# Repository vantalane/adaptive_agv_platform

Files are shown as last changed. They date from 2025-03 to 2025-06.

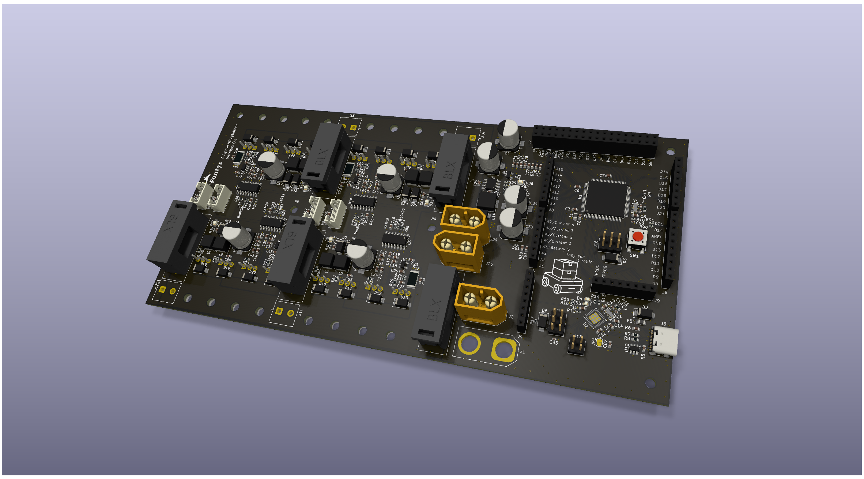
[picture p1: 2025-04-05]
design_sources/KiCAD/controller_mainboard_v0_1/controller_mainboard_visual.png

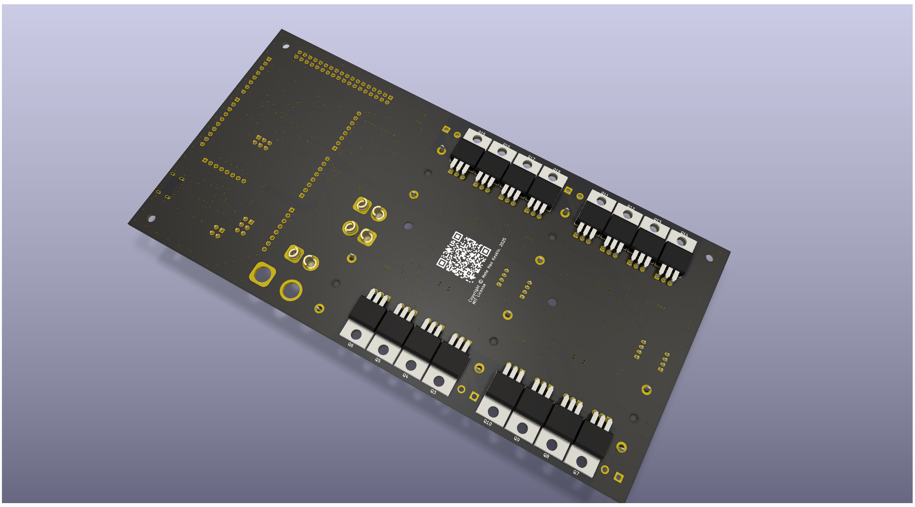
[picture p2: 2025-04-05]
design_sources/KiCAD/controller_mainboard_v0_1/controller_mainboard_visual_bottom.png

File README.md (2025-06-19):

# adaptive_agv_platform
Fontys adaptive robotics AGV platform design repository.

## Design files roadmap

Specifications and board information can be found in the "documentation" folder.

Design sources are aptly placed within design_sources folder. These include kicad files, production files and example code.

## PCBA production

Necessary files and information regarding ordering, assembly and part sourcing are packaged together with PCB versions.

These files can be found within 
``` design_sources/KiCAD/controller_mainboard_vX/production``` \
with ```vX``` being version number.

Instruction for production are found within the ```production``` folder. 
Currently, only V0.1 is available.

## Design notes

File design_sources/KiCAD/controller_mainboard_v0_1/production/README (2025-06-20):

Production files generated by use of Fabrication Toolkit by bennymeg

Order instructions for FONTYS.

PCB is designed with part availability of LCSC and Tinytronics.
The PCB will be assembled by using JLC PCBA service, the order procedure is similar to ordering only PCB's, but with some additions to it.

Steps

1- 
Load the controller_mainboard.zip on the jlcpcb order page.

2- 
From top to bottom, select the following settings:
base material: FR4
layers: 4
Dimensions are automatically filled (200x100mm)
QTY: 5 (This version 0.1 is deemed a prototype, therefore should always be validated before larger orders (a.k.a, buy the V1 largescale))
product type: industrial/consumer

different design: 1
Delivery format: single pcb
thickness: 1.6mm
color: (up to you, green is cheapest and fastest, but purple fits Fontys theme)
Silk: white
Materiel type: FR4-std TG 135-140
Surface finish: LeadFree HASL

Outer copper weight: 1oz
inner copper weight: 0.5oz
Layer sequence: yes
	L1 - controller_mainboard-F_Cu.gtl
	L2 - controller_mainboard-In1_Cu.g1
	L3 - controller_mainboard-In2_Cu.g2
	L4 - controller_mainboard-B_Cu.gbl
Specify stackup: yes - JLC04161H-7628
Via covering: plugged
Min via diameter: 0.3mm/(0.4/0.45mm)
Outline tolerance: regular
Confirm prod file: No
Mark on PCB: Order number
Gold Fingers: no
Castellated hole:no
pressfit hole: no
edge plating: no
Blind slots: no

3- 
Select "PCB Assembly" by using the button.

Fill in the following settings for PCB assembly:

PCBA type: Eco
Assembly side: Top
PCBA QTY: 2
Tooling holes: JLCPCB
Confirm part placement: Yes
Stencil storage: no 
Fixture Storage: no
Parts Selection: customer

*Dont fill in advanced options*
*ignore stencil*

4- 
Proceed by clicking on the "NEXT" button

5-
Now you should get a render of the PCB, proceed by clicking next
*photo here*

6-
Add bom file: bom.csv
Add CPL file: positions.csv
Go to next page after upload.

7- 
Most necessary parts should be automatically automatically selected. If certain parts are out of stock, and therefore are automatically not selected, alternative parts will need to be provided.
In this case, contact an experienced EE or me (m.keskin@student.fontys.nl or mete@kestech.net) for support.

All, EXCEPT for the following should be selected:
*XT-60 AMASS CONNECTOR J2,J25

Thus, at the top of the page you should have:
Total 40 parts detected, 35 parts confirmed, 10 parts not selected

The following are automatically not selected for assembly, 
J1
J7
J8 
J10,J4,J5,J6,J9
J11,J12,J13,J14
J16,J19
J18
J20,J21,J22,J23

Click on "NEXT" and after this "Do not place".

8- 
Now, a render of the PCB files should be displayed. 
*photo*
Click "NEXT".

9- 
On the Quote & order 
Select product description as - Research\Education\DIY\Entertainment > Robot - HS Code 847990

10- Pay

11- After JLC, there are certain parts that will be manually assembled onto the PCB. These are described in the "controller_board_v0_1.ods" spreadsheet file. Here, parts per PCB are described, order multiples of this set according to how many PCB's are going to be assembled.

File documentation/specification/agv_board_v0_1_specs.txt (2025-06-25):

Summary of board capabilites.

PCBA power:
	Battery voltage range: 8.5V - 15V
	Supply current abs max: 20A
	Supply current typical max: 15.2A

	Note: Power supplied by USB-C only powers the microcontrollers and certain current measurement IC's. Avoid powering high power devices through USB. 
 
Safety:
	Emergency stop: A male XT-60 connector is used to pass-through power supplied by a battery. A normally-closed high current emergency stop button should be used to short the terminals of connector J25. If this isn't connected, the battery will be practically "disconnected".

Motor drivers:
	Supply current: 5A absolute max, 3,8A typical max
	Driver voltage: Same as the battery voltage supplying board.
	
Motor current measurement:
	Measured until 5A max
	Voltage per Amp ratio: 1 V/A
	Vcurrent low-pass frequency cutoff(-3db point): 795.77 Hz 

Battery voltage measurement:
	Voltage divider ratio: 0.3377
		Example: Battery is 13.89 volts, Atmega ADC measures 13.89*0.3377=4.69V

Pins described below are additional information or explicit override of the Arduino mega board pins.
The AAP board allocates some GPIO for certain tasks.

Allocated GPIO of Atmega2560:

#Encoder pinouts
D22	ENC_B4
D23	ENC_A4
D24	ENC_B3
D25	ENC_A3
D26	ENC_B2
D27	ENC_A2
D28	ENC_B1
D29	ENC_B1

#Motor driver PWM pinouts
D2	MOT_DRV_PWM_B4
D3	MOT_DRV_PWM_A4
D4	MOT_DRV_PWM_B2
D5	MOT_DRV_PWM_A2
D6	MOT_DRV_PWM_A3
D7	MOT_DRV_PWM_B3
D8	MOT_DRV_PWM_A1
D9	MOT_DRV_PWM_B1

ADC3	VBAT_ADC
ADC4	MOT_CURR_V_1
ADC5	MOT_CURR_V_2
ADC6	MOT_CURR_V_3
ADC7	MOT_CURR_V_4

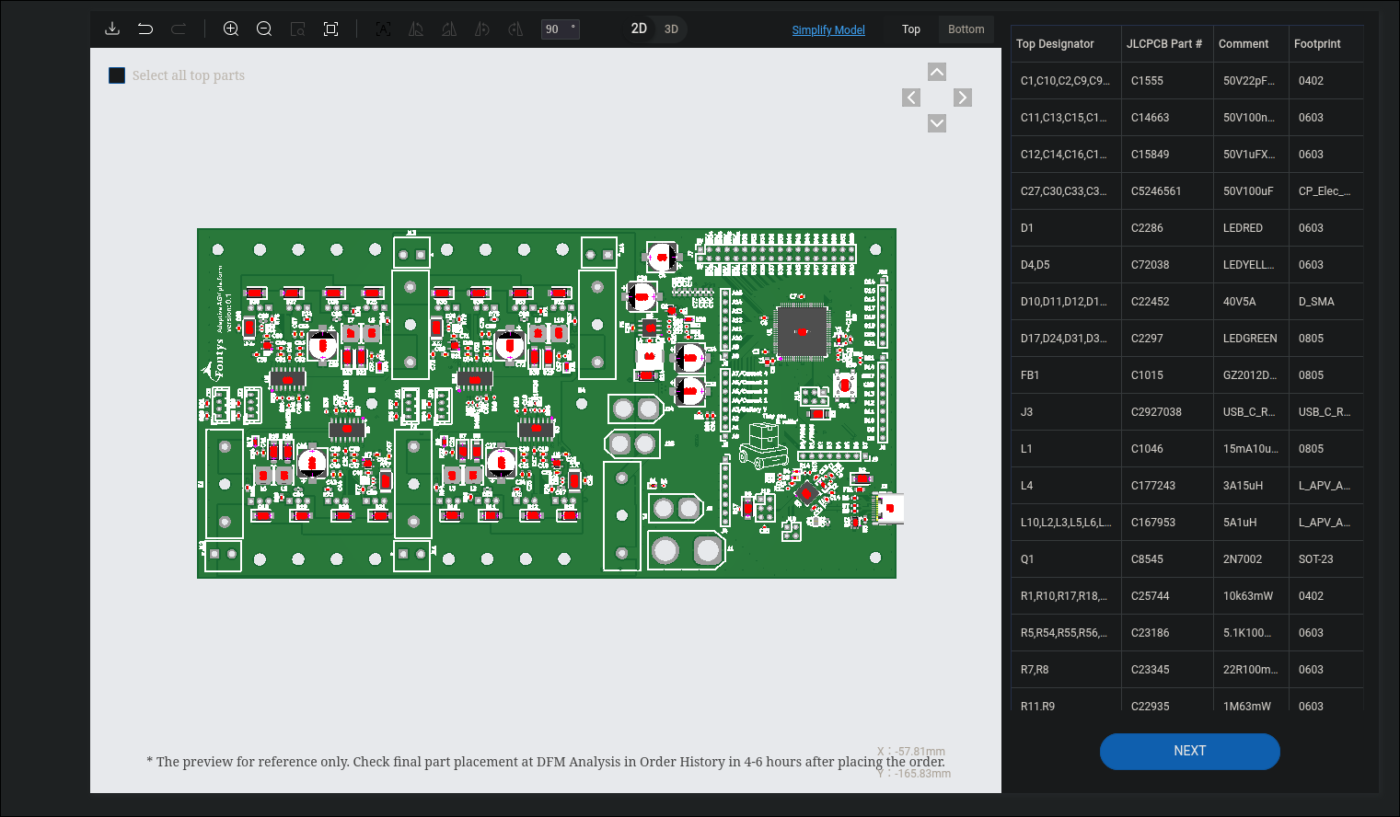
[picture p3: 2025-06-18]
documentation/media/pcba_overview_jlcpcb.png

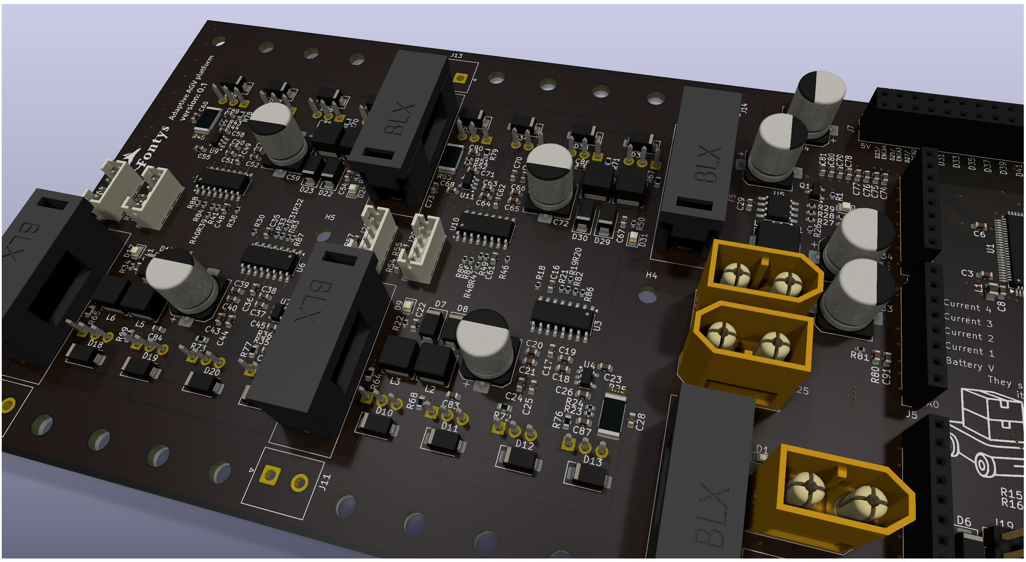
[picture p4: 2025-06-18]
documentation/media/pcba_v1_cool_render.png

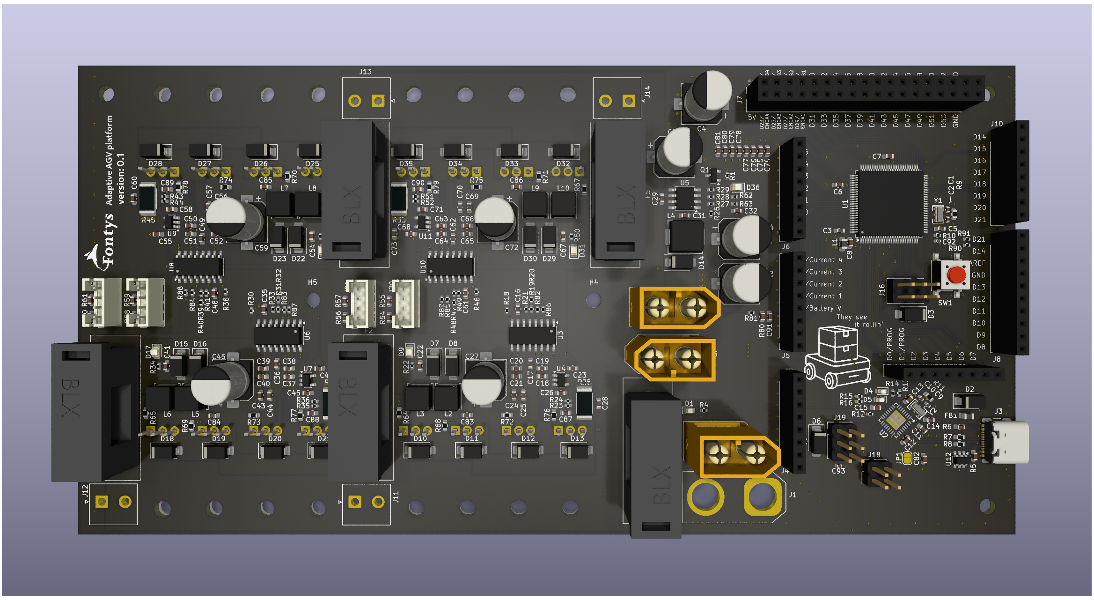
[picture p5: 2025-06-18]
documentation/media/pcba_v1_front_render.png

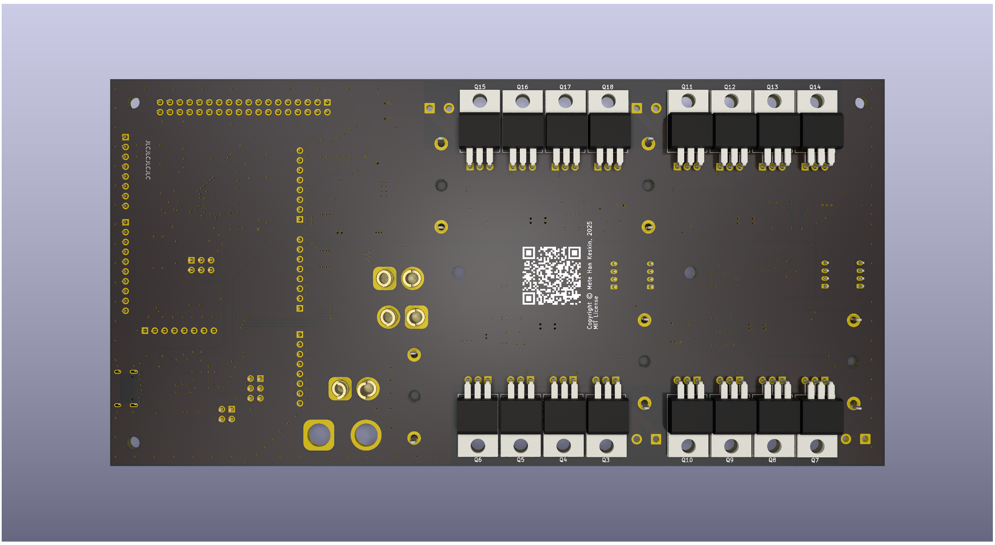
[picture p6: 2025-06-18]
documentation/media/pcba_v1_back_render.png

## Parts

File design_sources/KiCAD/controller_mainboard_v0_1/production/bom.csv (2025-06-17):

Designator | Footprint | Quantity | Value | LCSC Part #
C1, C10, C2, C9, C92, C93 | 0402 | 6 | 50V 22pF C0G | C1555
C11, C13, C15, C17, C23, C26, C28, C3, C31, C36, C42, C45, C47, C49, C5, C55, C58, C6, C60, C62, C68, C71, C73, C8, C91 | 0603 | 25 | 50V 100nF X7R | C14663
C12, C14, C16, C18, C19, C20, C21, C22, C24, C25, C29, C32, C35, C37, C38, C39, C40, C41, C43, C44, C48, C50, C51, C52, C53, C54, C56, C57, C61, C63, C64, C65, C66, C67, C69, C7, C70 | 0603 | 37 | 50V 1uF X5R | C15849
C27, C30, C33, C34, C4, C46, C59, C72 | CP_Elec_8x10.5 | 8 | 50V 100uF | C5246561
D1 | 0603 | 1 | LED RED | C2286
D10, D11, D12, D13, D14, D15, D16, D18, D19, D2, D20, D21, D22, D23, D25, D26, D27, D28, D29, D3, D30, D32, D33, D34, D35, D6, D7, D8 | D_SMA | 28 | 40V 5A | C22452
D17, D24, D31, D36, D9 | 0805 | 5 | LED GREEN | C2297
D4, D5 | 0603 | 2 | LED YELLOW | C72038
F1 | BLX-A fuse holder | 1 | Fuse 20A
F2, F3, F4, F5 | BLX-A fuse holder | 4 | 5A
FB1 | 0805 | 1 | GZ2012D101TF | C1015
J1 | XT-90_Connector | 1 | XT-90
J10, J4, J5, J6, J9 | PinSocket_1x08_P2.54mm_Vertical | 5 | 01x08_2.54mm _socket
J11, J12, J13, J14 | JST_NV_B02P-NV_1x02_P5.00mm_Vertical | 4 | 2P_screw_term
J16, J19 | PinHeader_2x03_P2.54mm_Vertical | 2 | 02x03_pinheader
J18 | PinHeader_2x02_P2.54mm_Vertical | 1 | 02x02_pinheader
J2, J25 | AMASS_XT60-M_1x02_P7.20mm_Vertical | 2 | XT-60
J20, J21, J22, J23 | JST_PH_B4B-PH-K_1x04_P2.00mm_Vertical | 4 | 01x04_JST_PH
J3 | USB_C_Receptacle_GCT_USB4105-xx-A_16P_TopMnt_Horizontal | 1 | USB_C_Receptacle_USB2.0_16P | C2927038
J7 | PinSocket_2x18_P2.54mm_Vertical | 1 | 02x18_2.54mm_socket
J8 | PinSocket_1x10_P2.54mm_Vertical | 1 | Conn_01x10_2.54mm_socket
L1 | 0805 | 1 | 15mA 10uH 1.15Ohm | C1046
L10, L2, L3, L5, L6, L7, L8, L9 | L_APV_ANR5040 | 8 | 5A 1uH | C167953
L4 | L_APV_APH0630 | 1 | 3A 15uH | C177243
Q1 | SOT-23 | 1 | 2N7002 | C8545
Q10, Q11, Q12, Q13, Q14, Q15, Q16, Q17, Q18, Q3, Q4, Q5, Q6, Q7, Q8, Q9 | TO-220-3_Horizontal_TabDown | 16 | IRF3205 | C2561
R1, R10, R17, R18, R19, R20, R26, R27, R28, R29, R30, R31, R32, R38, R39, R40, R46, R47, R48, R81, R82, R83, R84, R85, R86, R87, R88, R89, R90, R91 | 0402 | 30 | 10k 63mW | C25744
R11, R9 | 0603 | 2 | 1M 63mW | C22935
R12, R13, R14, R15, R16, R22, R23, R24, R34, R35, R36, R4, R42, R43, R44, R50, R51, R52, R62, R63 | 0402 | 20 | 1k 63mW | C11702
R25, R37, R45, R53 | 2512 | 4 | 50m 750mW 1% | C127698
R5, R54, R55, R56, R57, R58, R59, R6, R60, R61, R80 | 0603 | 11 | 5.1K 100mW | C23186
R64, R65, R66, R67, R68, R69, R70, R71, R72, R73, R74, R75, R76, R77, R78, R79 | 0603 | 16 | 0R 100mW | C21189
R7, R8 | 0603 | 2 | 22R 100mW | C23345
SW1 | SW_SPST_PTS645 | 1 | SW_Push | C19191552
U1 | TQFP-100_14x14mm_P0.5mm | 1 | ATmega2560-16A | C22460
U10, U3, U6, U8 | SOIC-16_3.9x9.9mm_P1.27mm | 4 | HIP4082IBZT | C50123
U11, U4, U7, U9 | SOT-23-5 | 4 | INA180A1IDBVR | C122228
U12 | SOT-23-6 | 1 | USBLC6-4SC6 | C5180279
U2 | QFN-32-1EP_5x5mm_P0.5mm_EP3.1x3.1mm | 1 | ATmega16U2-M | C17317
U5 | TI_SO-PowerPAD-8_ThermalVias | 1 | TPS5430DDA | C9864
Y1, Y2 | Resonator_SMD_Murata_CSTxExxV-3Pin_3.0x1.1mm | 2 | 16MHz | C783275

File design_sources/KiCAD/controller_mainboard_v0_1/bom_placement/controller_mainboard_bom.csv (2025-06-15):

Id | Designator | Footprint | Quantity | Designation | Supplier and ref
1 | U12 | SOT-23-6 | 1 | USBLC6-4SC6
2 | C11,C47,C45,C5,C42,C3,C6,C68,C26,C15,C8,C60,C13,C58,C71,C23,C91,C62,C17,C55,C36,C31,C49,C28,C73 | C_0603_1608Metric | 25 | 50V 100nF X7R
3 | J6,J5,J9,J4,J10 | PinSocket_1x08_P2.54mm_Vertical | 5 | 01x08_2.54mm _socket
4 | R17,R29,R30,R82,R85,R20,R28,R47,R46,R88,R10,R27,R31,R39,R48,R40,R19,R81,R26,R32,R1,R86,R84,R90,R87,R38,R91,R83,R18,R89 | R_0402_1005Metric | 30 | 10k 63mW
5 | D21,D8,D34,D33,D18,D22,D12,D26,D28,D15,D19,D10,D27,D25,D20,D11,D14,D35,D32,D23,D30,D16,D7,D3,D6,D13,D2,D29 | D_SMA | 28 | 40V 5A
6 | J16,J19 | PinHeader_2x03_P2.54mm_Vertical | 2 | 02x03_pinheader
7 | C82,C85,C78,C89,C83,C90,C88,C74,C87,C84,C80,C76,C79,C75,C77,C81,C86 | C_0603_1608Metric | 17 | N.C.
8 | U7,U4,U11,U9 | SOT-23-5 | 4 | INA180A1IDBVR
9 | C53,C65,C20,C56,C52,C14,C66,C24,C18,C50,C54,C35,C22,C43,C37,C70,C12,C19,C63,C67,C32,C40,C41,C16,C7,C57,C25,C61,C38,C29,C51,C64,C21,C44,C39,C69,C48 | C_0603_1608Metric | 37 | 50V 1uF X5R
10 | D17,D31,D36,D24,D9 | LED_0805_2012Metric | 5 | LED GREEN
11 | R33,R49,R41,R21 | R_0402_1005Metric | 4 | N.C.
12 | L3,L2,L9,L5,L10,L7,L8,L6 | L_APV_ANR5040 | 8 | 5A 1uH
13 | C1,C2,C93,C92,C9,C10 | C_0402_1005Metric | 6 | 50V 22pF C0G
14 | R15,R34,R50,R24,R44,R14,R63,R43,R52,R23,R42,R36,R62,R12,R16,R4,R22,R35,R51,R13 | R_0402_1005Metric | 20 | 1k 63mW
15 | F2,F4,F3,F5 | BLX-A fuse holder | 4 | 5A
16 | C46,C34,C4,C59,C27,C30,C33,C72 | CP_Elec_8x10.5 | 8 | 50V 100uF
17 | J12,J13,J14,J11 | JST_NV_B02P-NV_1x02_P5.00mm_Vertical | 4 | 2P_screw_term
18 | R60,R56,R54,R57,R6,R59,R61,R58,R80,R55,R5 | C_0603_1608Metric | 11 | 5.1K 100mW
19 | D1 | LED_0603_1608Metric | 1 | LED RED
20 | F1 | BLX-A fuse holder | 1 | Fuse 20A
21 | U6,U3,U8,U10 | SOIC-16_3.9x9.9mm_P1.27mm | 4 | HIP4082IBZT
22 | U5 | TI_SO-PowerPAD-8_ThermalVias | 1 | TPS5430DDA
23 | J25,J2,J24 | AMASS_XT60-M_1x02_P7.20mm_Vertical | 3 | XT-60
24 | D5,D4 | LED_0603_1608Metric | 2 | LED YELLOW
25 | R76,R66,R64,R71,R78,R74,R69,R75,R72,R67,R70,R77,R68,R79,R65,R73 | R_0603_1608Metric | 16 | 0R 100mW
26 | J22,J21,J23,J20 | JST_PH_B4B-PH-K_1x04_P2.00mm_Vertical | 4 | 01x04_JST_PH
27 | L1 | L_0805_2012Metric | 1 | 15mA 10uH 1.15Ohm
28 | Q1 | SOT-23 | 1 | 2N7002
29 | R37,R25,R53,R45 | R_2512_6332Metric | 4 | 50m 750mW 1%
30 | Y1,Y2 | Resonator_SMD_Murata_CSTxExxV-3Pin_3.0x1.1mm | 2 | 16MHz
31 | U2 | QFN-32-1EP_5x5mm_P0.5mm_EP3.1x3.1mm | 1 | ATmega16U2-M
32 | U1 | TQFP-100_14x14mm_P0.5mm | 1 | ATmega2560-16A
33 | J8 | PinSocket_1x10_P2.54mm_Vertical | 1 | Conn_01x10_2.54mm_socket
34 | J1 | XT-90_Connector | 1 | XT-90
35 | R7,R8 | R_0603_1608Metric | 2 | 22R 100mW
36 | SW1 | SW_SPST_PTS645 | 1 | SW_Push
37 | J3 | USB_C_Receptacle_GCT_USB4105-xx-A_16P_TopMnt_Horizontal | 1 | USB_C_Receptacle_USB2.0_16P
38 | J7 | PinSocket_2x18_P2.54mm_Vertical | 1 | 02x18_2.54mm_socket
39 | L4 | L_APV_APH0630 | 1 | 3A 15uH
40 | R9,R11 | R_0603_1608Metric | 2 | 1M 63mW
41 | J18 | PinHeader_2x02_P2.54mm_Vertical | 1 | 02x02_pinheader
42 | FB1 | L_0805_2012Metric | 1 | GZ2012D101TF
43 | Q9,Q4,Q8,Q6,Q11,Q14,Q13,Q7,Q15,Q10,Q18,Q3,Q16,Q5,Q12,Q17 | TO-220-3_Horizontal_TabDown | 16 | IRF3205

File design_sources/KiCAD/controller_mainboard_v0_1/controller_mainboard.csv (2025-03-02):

Reference | Qty | JLCPCB | Value | DNP | Exclude from BOM | Exclude from Board | Footprint | Datasheet
C1,C2,C8,C9 | 4 | C1555 | 50V 22pF C0G |  |  |  | Capacitor_SMD:C_0402_1005Metric | https://jlcpcb.com/api/file/downloadByFileSystemAccessId/8579707297419231232
C3,C6,C11,C13,C19,C20,C22,C23,C24,C25,C26,C27,C33,C34 | 14 | C15849 | 50V 1uF X5R |  |  |  | Capacitor_SMD:C_0603_1608Metric | https://jlcpcb.com/api/file/downloadByFileSystemAccessId/8556213788459761664
C4,C5,C7,C10,C12,C14,C15,C16,C17,C18,C28,C29 | 12 | C14663 | 50V 100nF X7R |  |  |  | Capacitor_SMD:C_0603_1608Metric | https://jlcpcb.com/api/file/downloadByFileSystemAccessId/8579707083955945472
C21,C30,C31,C32 | 4 | C5246561 | 50V 100uF |  |  |  | Capacitor_SMD:CP_Elec_8x10.5 | ~
D1,D2,D5,D6,D7,D8,D9,D10,D11,D12 | 10 | C22452 | 40V 5A |  |  |  | Diode_SMD:D_SMA | https://jlcpcb.com/api/file/downloadByFileSystemAccessId/8579707587489042432
D3,D4 | 2 | C72038 | LED YELLOW |  |  |  | LED_SMD:LED_0603_1608Metric | ~
F1 | 1 |  | Fuse 20A |  |  |  | Custom_feetprint:BLX-A fuse holder | ~
F2 | 1 |  | 5A |  |  |  | Custom_feetprint:BLX-A fuse holder | ~
FB1 | 1 | C1015 | GZ2012D101TF |  |  |  | Inductor_SMD:L_0805_2012Metric | https://jlcpcb.com/api/file/downloadByFileSystemAccessId/8579709135115370496
J1,J4 | 2 |  | 02x03_pinheader |  |  |  | Connector_PinHeader_2.54mm:PinHeader_2x03_P2.54mm_Vertical | ~
J2 | 1 |  | 01x05_Socket | DNP | Excluded from BOM |  |  | ~
J3 | 1 |  | 02x02_pinheader |  |  |  |  | ~
J5 | 1 |  | XT-90 |  |  |  |  | ~
J6 | 1 |  | USB_C_Receptacle_USB2.0_16P |  |  |  |  | https://www.usb.org/sites/default/files/documents/usb_type-c.zip
J7 | 1 |  | XT-60 |  |  |  |  | ~
JP2 | 1 |  | SolderJumper_2_Open |  | Excluded from BOM |  | Jumper:SolderJumper-2_P1.3mm_Open_RoundedPad1.0x1.5mm | ~
L1 | 1 | C1046 | 15mA 10uH 1.15Ohm |  |  |  | Inductor_SMD:L_0805_2012Metric | ~
L2,L3 | 2 | C167953 | 5A 1uH |  |  |  |  | ~
L4 | 1 | C177243 | 3A 15uH |  |  |  |  | ~
Q1,Q2,Q3,Q4 | 4 | C2561 | IRF3205 |  |  |  | Package_TO_SOT_THT:TO-220-3_Vertical | http://www.irf.com/product-info/datasheets/data/irf3205.pdf
Q5 | 1 | C8545 | 2N7002 |  |  |  | Package_TO_SOT_SMD:SOT-23 | https://www.onsemi.com/pub/Collateral/NDS7002A-D.PDF
R1,R9,R13,R14,R16,R19,R20,R21,R22,R23 | 10 | C25744 | 10k 63mW |  |  |  | Resistor_SMD:R_0402_1005Metric | https://jlcpcb.com/api/file/downloadByFileSystemAccessId/8556212101498380288
R2,R8 | 2 |  | 1M 63mW |  |  |  | Resistor_SMD:R_0603_1608Metric | ~
R3,R4,R5,R6,R7,R11,R12 | 7 | C11702 | 1k 63mW |  |  |  | Resistor_SMD:R_0402_1005Metric
R10 | 1 | C620706 | 50m 750mW 1% |  |  |  | Resistor_SMD:R_2512_6332Metric | ~
R15 | 1 | C25744 | N.C. | DNP |  |  | Resistor_SMD:R_0402_1005Metric | https://jlcpcb.com/api/file/downloadByFileSystemAccessId/8556212101498380288
R17,R18 | 2 | C23345 | 22R 100mW |  |  |  | Resistor_SMD:R_0603_1608Metric | ~
U1 | 1 |  | ATmega2560-16A |  |  |  | Package_QFP:TQFP-100_14x14mm_P0.5mm | http://ww1.microchip.com/downloads/en/DeviceDoc/Atmel-2549-8-bit-AVR-Microcontroller-ATmega640-1280-1281-2560-2561_datasheet.pdf
U2 | 1 |  | ATmega16U2-M |  |  |  | Package_DFN_QFN:QFN-32-1EP_5x5mm_P0.5mm_EP3.1x3.1mm | http://ww1.microchip.com/downloads/en/DeviceDoc/doc7799.pdf
U3 | 1 | C50123 | HIP4082IBZT |  |  |  | Package_SO:SOIC-16_3.9x9.9mm_P1.27mm | https://www.renesas.com/www/doc/datasheet/hip4082.pdf
U4 | 1 | C122228 | INA180A1IDBVR |  |  |  | Package_TO_SOT_SMD:SOT-23-5 | http://www.ti.com/lit/ds/symlink/ina180.pdf
U5 | 1 | C9864 | TPS5430DDA |  |  |  | Package_SO:TI_SO-PowerPAD-8_ThermalVias | http://www.ti.com/lit/ds/symlink/tps5430.pdf
Y2,Y3 | 2 | C783275 | 16MHz |  |  |  | Crystal:Resonator_SMD_Murata_CSTxExxV-3Pin_3.0x1.1mm | ~

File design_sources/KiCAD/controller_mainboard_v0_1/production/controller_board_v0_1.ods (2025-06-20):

PART MFR | DESC. | QTY (P/PCB) | SELLER | ALL QTY COST | PART COST (ex BTW) | URL
005974 | JST-PH 4P cable | 4 | Tinytronics | 2.64 | 0.66 | https://www.tinytronics.nl/en/cables-and-connectors/cables-and-adapters/jst-compatible/jst-ph-female-to-dupont-female-compatible-cable-4p-15cm
001195 | Fuse holder 5x20mm - 5A – PCB | 5 | Tinytronics | 2.05 | 0.41 | https://www.tinytronics.nl/en/components/fuses/fuse-holder-5x20mm-5a-pcb
000504 | 8 Pins header Female | 5 | Tinytronics | 0.9 | 0.18 | https://www.tinytronics.nl/en/cables-and-connectors/connectors/pin-headers/female/8-pins-header-female
001181 | 2x18 Pins header Female | 1 | Tinytronics | 0.36 | 0.36 | https://www.tinytronics.nl/en/cables-and-connectors/connectors/pin-headers/female/2x18-pins-header-female
000506 | 10 Pins header Female | 1 | Tinytronics | 0.21 | 0.21 | https://www.tinytronics.nl/en/cables-and-connectors/connectors/pin-headers/female/10-pins-header-female
000170 | 2 Pin Screw Terminal Block Connector 5.08mm Distance | 4 | Tinytronics | 2.48 | 0.62 | https://www.tinytronics.nl/en/cables-and-connectors/connectors/screw-terminals/2-pin-screw-terminal-block-connector-5.08mm-distance
 | 2x3 male pins | 2 | T.B.D | 0
 | 2x2 male pins | 1 | T.B.D | 0
002382 | XT60U connector set | 2 | Tinytronics | 1.48 | 0.74
 |  |  |  | 0
 |  |  |  | 0
 |  |  |  | 0
 |  |  |  | 0
 |  |  |  | 0
 |  |  |  | 0
 |  |  |  | 0
 |  |  |  | 0
 |  |  |  | 0
 |  |  |  | 0
Total cost of 1 PCB | 10.12

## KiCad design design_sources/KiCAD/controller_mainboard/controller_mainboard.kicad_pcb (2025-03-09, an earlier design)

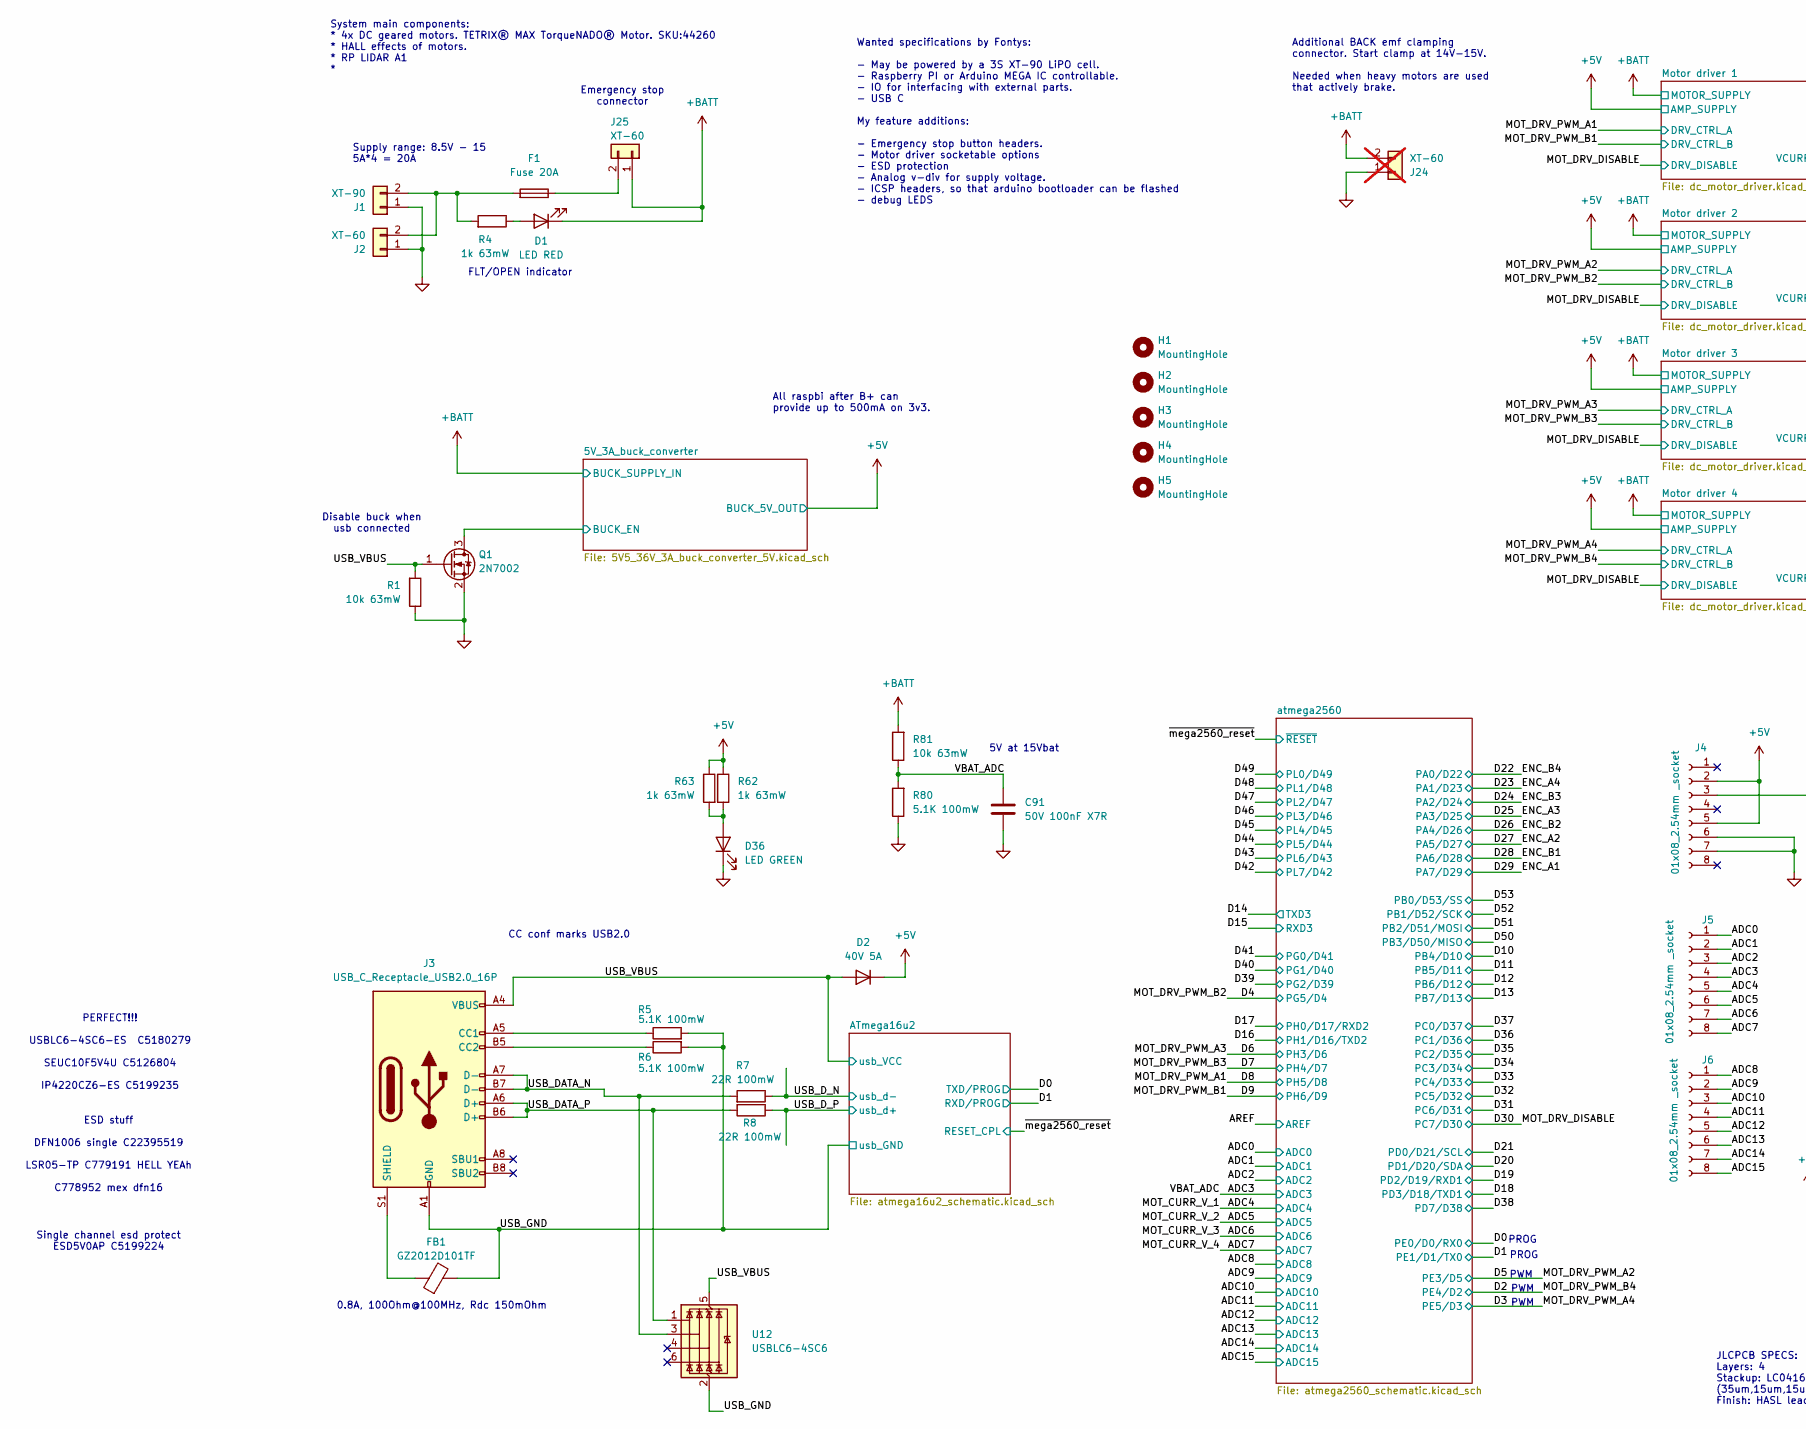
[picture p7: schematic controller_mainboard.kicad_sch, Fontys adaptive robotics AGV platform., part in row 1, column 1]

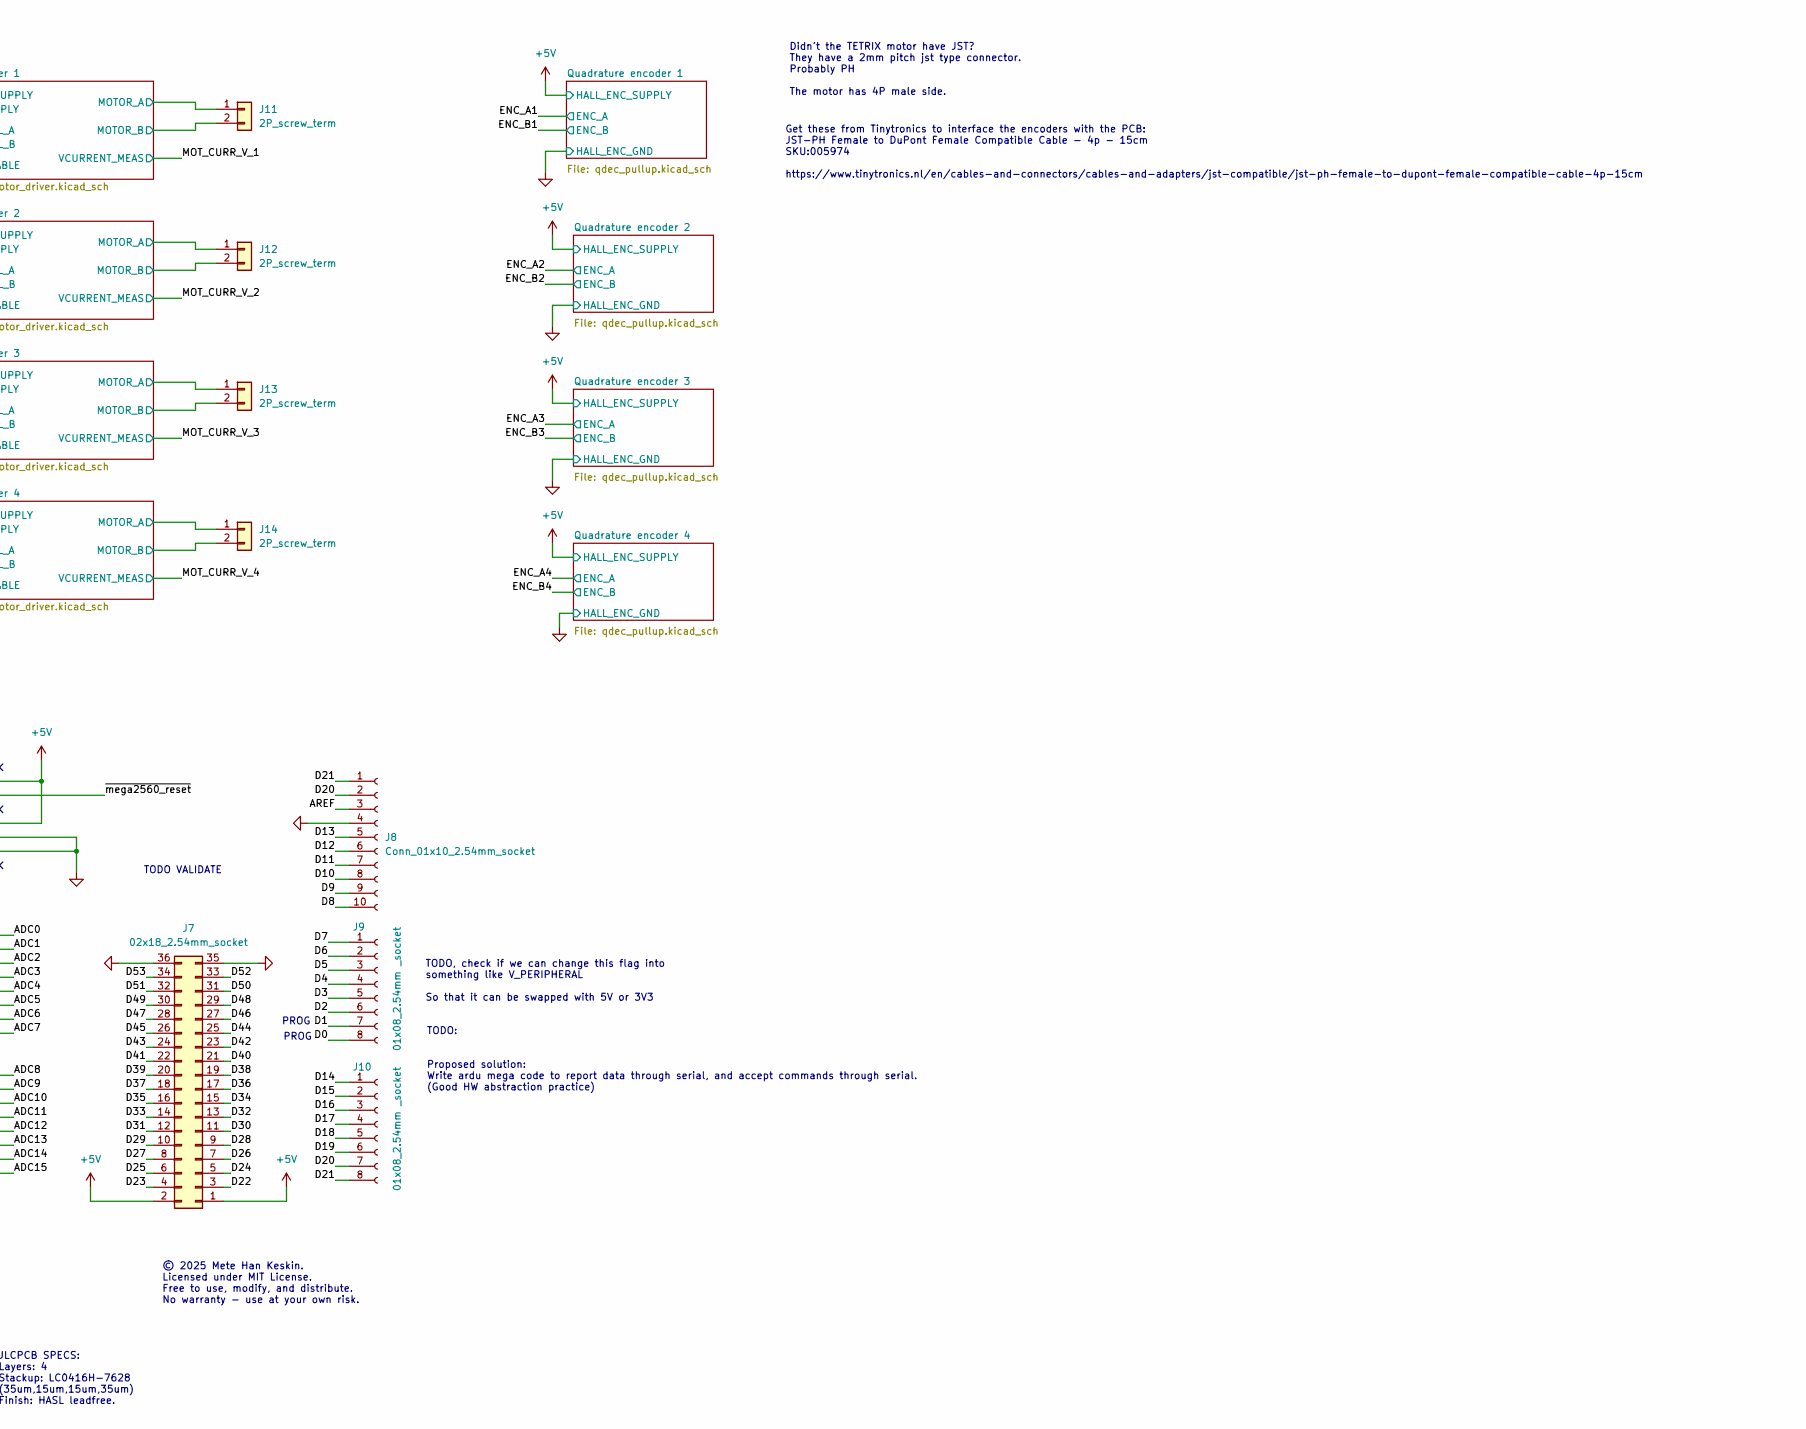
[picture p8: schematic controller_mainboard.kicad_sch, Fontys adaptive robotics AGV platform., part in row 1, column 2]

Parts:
C91: 50V 100nF X7R; C_0603_1608Metric; LCSC C14663
D1: LED RED; LED_0603_1608Metric; LCSC C2286
D2: 40V 5A; D_SMA; LCSC C22452
D36: LED GREEN; LED_0805_2012Metric; LCSC C2297
F1: Fuse 20A; BLX-A fuse holder
FB1: GZ2012D101TF; L_0805_2012Metric; LCSC C1015
H1, H2, H3, H4, H5: MountingHole; MountingHole_3.2mm_M3_DIN965
J1: XT-90; XT-90_Connector
J2: XT-60; AMASS_XT60-M_1x02_P7.20mm_Vertical
J3: USB_C_Receptacle_USB2.0_16P; USB_C_Receptacle_GCT_USB4105-xx-A_16P_TopMnt_Horizontal; LCSC C2927038
J4, J5, J6, J9, J10: 01x08_2.54mm _socket; PinSocket_1x08_P2.54mm_Vertical
J7: 02x18_2.54mm_socket; PinSocket_2x18_P2.54mm_Vertical
J8: Conn_01x10_2.54mm_socket; PinSocket_1x10_P2.54mm_Vertical
J11, J12, J13, J14: 2P_screw_term; JST_NV_B02P-NV_1x02_P5.00mm_Vertical
J24: XT-60; AMASS_XT60-F_1x02_P7.20mm_Vertical; not fitted
J25: XT-60; AMASS_XT60-F_1x02_P7.20mm_Vertical
Q1: 2N7002; SOT-23; LCSC C8545
R1, R81: 10k 63mW; R_0402_1005Metric; LCSC C25744
R4, R62, R63: 1k 63mW; R_0402_1005Metric; LCSC C11702
R5, R6, R80: 5.1K 100mW; C_0603_1608Metric; LCSC C23186
R7, R8: 22R 100mW; R_0603_1608Metric; LCSC C23345
U12: USBLC6-4SC6; SOT-23-6; LCSC C5180279

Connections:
+5V: D2.1 (K), J4.2, J4.5, J7.1, J7.2, R62.1, R63.1; also elsewhere on the board
+BATT: D1.1 (K), J24.2, J25.1, R81.2; also elsewhere on the board
/5V_3A_buck_converter/BUCK_EN: Q1.3 (D); also elsewhere on the board
/ADC0: J5.1; also elsewhere on the board
/ADC1: J5.2; also elsewhere on the board
/ADC2: J5.3; also elsewhere on the board
/ADC4: J5.5; also elsewhere on the board
/ADC5: J5.6; also elsewhere on the board
/ADC6: J5.7; also elsewhere on the board
/ADC7: J5.8; also elsewhere on the board
/ADC8: J6.1; also elsewhere on the board
/ADC9: J6.2; also elsewhere on the board
/ADC10: J6.3; also elsewhere on the board
/ADC11: J6.4; also elsewhere on the board
/ADC12: J6.5; also elsewhere on the board
/ADC13: J6.6; also elsewhere on the board
/ADC14: J6.7; also elsewhere on the board
/ADC15: J6.8; also elsewhere on the board
/AREF: J8.3; also elsewhere on the board
/D0: J9.8; also elsewhere on the board
/D1: J9.7; also elsewhere on the board
/D2: J9.6; also elsewhere on the board
/D3: J9.5; also elsewhere on the board
/D4: J9.4; also elsewhere on the board
/D5: J9.3; also elsewhere on the board
/D6: J9.2; also elsewhere on the board
/D7: J9.1; also elsewhere on the board
/D8: J8.10; also elsewhere on the board
/D9: J8.9; also elsewhere on the board
/D10: J8.8; also elsewhere on the board
/D11: J8.7; also elsewhere on the board
/D12: J8.6; also elsewhere on the board
/D13: J8.5; also elsewhere on the board
/D14: J10.1; also elsewhere on the board
/D15: J10.2; also elsewhere on the board
/D16: J10.3; also elsewhere on the board
/D17: J10.4; also elsewhere on the board
/D18: J10.5; also elsewhere on the board
/D19: J10.6; also elsewhere on the board
/D20: J8.2, J10.7; also elsewhere on the board
/D21: J8.1, J10.8; also elsewhere on the board
/D22: J7.3; also elsewhere on the board
/D23: J7.4; also elsewhere on the board
/D24: J7.5; also elsewhere on the board
/D25: J7.6; also elsewhere on the board
/D26: J7.7; also elsewhere on the board
/D27: J7.8; also elsewhere on the board
/D28: J7.9; also elsewhere on the board
/D29: J7.10; also elsewhere on the board
/D30: J7.11; also elsewhere on the board
/D31: J7.12; also elsewhere on the board
/D32: J7.13; also elsewhere on the board
/D33: J7.14; also elsewhere on the board
/D34: J7.15; also elsewhere on the board
/D35: J7.16; also elsewhere on the board
/D36: J7.17; also elsewhere on the board
/D37: J7.18; also elsewhere on the board
/D38: J7.19; also elsewhere on the board
/D39: J7.20; also elsewhere on the board
/D40: J7.21; also elsewhere on the board
/D41: J7.22; also elsewhere on the board
/D42: J7.23; also elsewhere on the board
/D43: J7.24; also elsewhere on the board
/D44: J7.25; also elsewhere on the board
/D45: J7.26; also elsewhere on the board
/D46: J7.27; also elsewhere on the board
/D47: J7.28; also elsewhere on the board
/D48: J7.29; also elsewhere on the board
/D49: J7.30; also elsewhere on the board
/D50: J7.31; also elsewhere on the board
/D51: J7.32; also elsewhere on the board
/D52: J7.33; also elsewhere on the board
/D53: J7.34; also elsewhere on the board
/Motor driver 1/MOT_SIDE_A: J11.1; also elsewhere on the board
/Motor driver 1/MOT_SIDE_B: J11.2; also elsewhere on the board
/Motor driver 2/MOT_SIDE_A: J12.1; also elsewhere on the board
/Motor driver 2/MOT_SIDE_B: J12.2; also elsewhere on the board
/Motor driver 3/MOT_SIDE_A: J13.1; also elsewhere on the board
/Motor driver 3/MOT_SIDE_B: J13.2; also elsewhere on the board
/Motor driver 4/MOT_SIDE_A: J14.1; also elsewhere on the board
/Motor driver 4/MOT_SIDE_B: J14.2; also elsewhere on the board
/USB_DATA_N: J3.A7 (D-), J3.B7 (D-), R7.2, U12.3 (I/O2)
/USB_DATA_P: J3.A6 (D+), J3.B6 (D+), R8.2, U12.1 (I/O1)
/USB_D_N: R7.1; also elsewhere on the board
/USB_D_P: R8.1; also elsewhere on the board
/USB_GND: FB1.2, J3.A1 (GND), J3.A12 (GND), J3.B1 (GND), J3.B12 (GND), R5.2, R6.2, U12.2 (GND); also elsewhere on the board
/USB_VBUS: D2.2 (A), J3.A4 (VBUS), J3.A9 (VBUS), J3.B4 (VBUS), J3.B9 (VBUS), Q1.1 (G), R1.2, U12.5 (VBUS); also elsewhere on the board
/~mega2560_reset: J4.3; also elsewhere on the board
GND: C91.1, D36.1 (K), J1.1, J2.1, J4.6, J4.7, J7.35, J7.36, J8.4, J24.1, Q1.2 (S), R1.1, R80.1; also elsewhere on the board
unnamed: D1.2 (A), R4.1
unnamed: D36.2 (A), R62.2, R63.2
unnamed: F1.2, J1.2, J2.2, R4.2
unnamed: J3.A5 (CC1), R5.1
unnamed: J3.B5 (CC2), R6.1
unnamed: FB1.1, J3.S1 (SHIELD)
unnamed: F1.1, J25.2

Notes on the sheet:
Get these from Tinytronics to interface the encoders with the PCB: JST-PH Female to DuPont Female Compatible Cable - 4p - 15cm SKU:005974 https://www.tinytronics.nl/en/cables-and-connectors/cables-and-adapters/jst-compatible/jst-ph-female-to-dupont-female-compatible-cable-4p-15cm
PROG
JLCPCB SPECS: Layers: 4 Stackup: LC0416H-7628 (35um,15um,15um,35um) Finish: HASL leadfree.
Emergency stop connector
Wanted specifications by Fontys: - May be powered by a 3S XT-90 LiPO cell. - Raspberry PI or Arduino MEGA IC controllable. - IO for interfacing with external parts. - USB C My feature additions: - Emergency stop button headers. - Motor driver socketable options - ESD protection - Analog v-div for s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
© 2025 Mete Han Keskin. Licensed under MIT License. Free to use, modify, and distribute. No warranty - use at your own risk.
5A*4 = 20A
PWM
ESD stuff DFN1006 single C22395519 LSR05-TP C779191 HELL YEAh C778952 mex dfn16
0.8A, 100Ohm@100MHz, Rdc 150mOhm
TODO VALIDATE
Supply range: 8.5V - 15
All raspbi after B+ can provide up to 500mA on 3v3.
FLT/OPEN indicator
CC conf marks USB2.0
System main components: * 4x DC geared motors. TETRIX® MAX TorqueNADO® Motor. SKU:44260 * HALL effects of motors. * RP LIDAR A1 *
Disable buck when usb connected
TODO: Proposed solution: Write ardu mega code to report data through serial, and accept commands through serial. (Good HW abstraction practice)
Didn't the TETRIX motor have JST? They have a 2mm pitch jst type connector. Probably PH The motor has 4P male side.
PERFECT!!! USBLC6-4SC6-ES C5180279 SEUC10F5V4U C5126804 IP4220CZ6-ES C5199235
5V at 15Vbat
TODO, check if we can change this flag into something like V_PERIPHERAL So that it can be swapped with 5V or 3V3
Single channel esd protect ESD5V0AP C5199224
Additional BACK emf clamping connector. Start clamp at 14V-15V. Needed when heavy motors are used that actively brake.

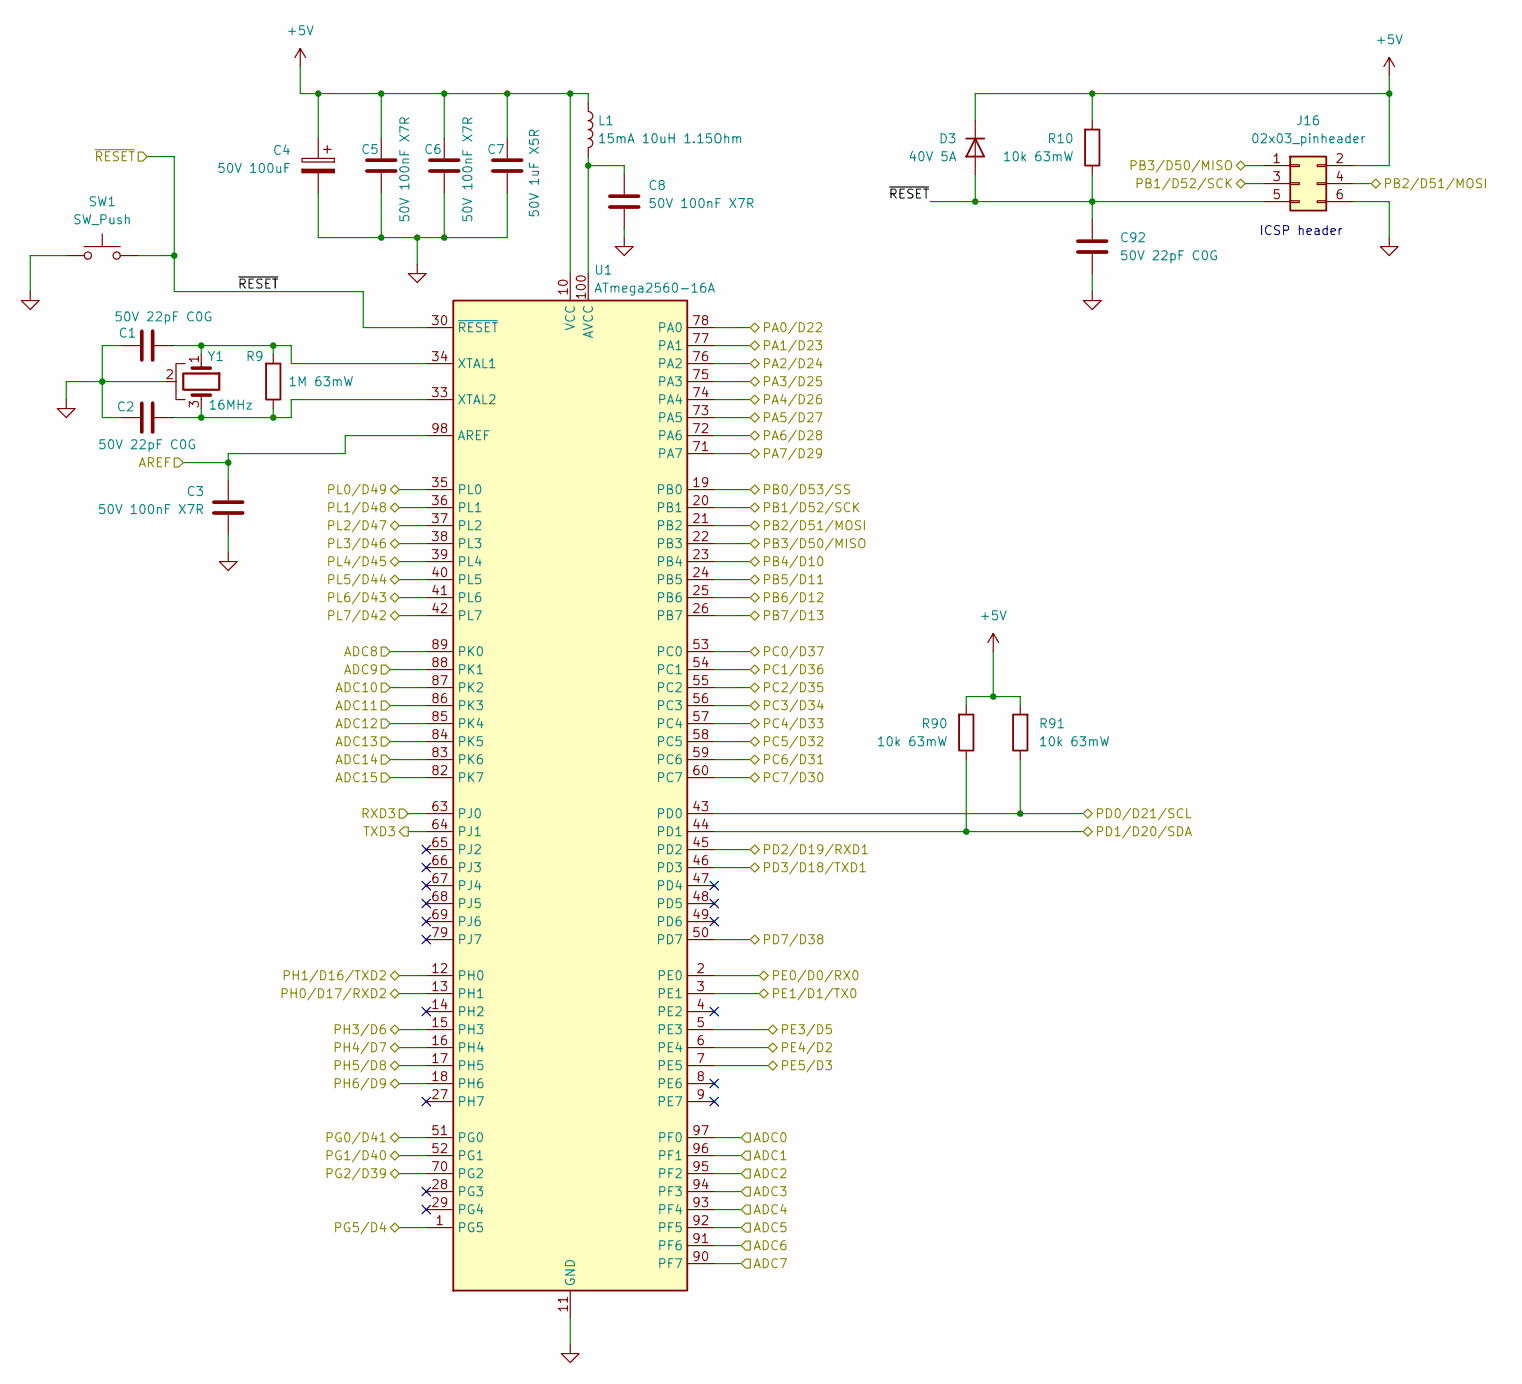
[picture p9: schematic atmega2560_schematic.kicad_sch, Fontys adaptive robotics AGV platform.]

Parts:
C1, C2, C92: 50V 22pF C0G; C_0402_1005Metric; LCSC C1555
C3, C5, C6, C8: 50V 100nF X7R; C_0603_1608Metric; LCSC C14663
C4: 50V 100uF; CP_Elec_8x10.5; LCSC C5246561
C7: 50V 1uF X5R; C_0603_1608Metric; LCSC C15849
D3: 40V 5A; D_SMA; LCSC C22452
J16: 02x03_pinheader; PinHeader_2x03_P2.54mm_Vertical
L1: 15mA 10uH 1.15Ohm; L_0805_2012Metric; LCSC C1046
R9: 1M 63mW; R_0603_1608Metric; LCSC C22935
R10, R90, R91: 10k 63mW; R_0402_1005Metric; LCSC C25744
SW1: SW_Push; SW_SPST_PTS645; LCSC C19191552
U1: ATmega2560-16A; TQFP-100_14x14mm_P0.5mm; LCSC C22460
Y1: 16MHz; Resonator_SMD_Murata_CSTxExxV-3Pin_3.0x1.1mm; LCSC C783275

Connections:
+5V: C4.1, C5.1, C6.1, C7.1, D3.1 (K), J16.2, L1.1, R10.2, R90.2, R91.2, U1.10 (VCC), U1.31 (VCC), U1.61 (VCC), U1.80 (VCC); also elsewhere on the board
/ADC0: U1.97 (PF0); also elsewhere on the board
/ADC1: U1.96 (PF1); also elsewhere on the board
/ADC2: U1.95 (PF2); also elsewhere on the board
/ADC4: U1.93 (PF4); also elsewhere on the board
/ADC5: U1.92 (PF5); also elsewhere on the board
/ADC6: U1.91 (PF6); also elsewhere on the board
/ADC7: U1.90 (PF7); also elsewhere on the board
/ADC8: U1.89 (PK0); also elsewhere on the board
/ADC9: U1.88 (PK1); also elsewhere on the board
/ADC10: U1.87 (PK2); also elsewhere on the board
/ADC11: U1.86 (PK3); also elsewhere on the board
/ADC12: U1.85 (PK4); also elsewhere on the board
/ADC13: U1.84 (PK5); also elsewhere on the board
/ADC14: U1.83 (PK6); also elsewhere on the board
/ADC15: U1.82 (PK7); also elsewhere on the board
/AREF: C3.1, U1.98 (AREF); also elsewhere on the board
/D0: U1.2 (PE0); also elsewhere on the board
/D1: U1.3 (PE1); also elsewhere on the board
/D2: U1.6 (PE4); also elsewhere on the board
/D3: U1.7 (PE5); also elsewhere on the board
/D4: U1.1 (PG5); also elsewhere on the board
/D5: U1.5 (PE3); also elsewhere on the board
/D6: U1.15 (PH3); also elsewhere on the board
/D7: U1.16 (PH4); also elsewhere on the board
/D8: U1.17 (PH5); also elsewhere on the board
/D9: U1.18 (PH6); also elsewhere on the board
/D10: U1.23 (PB4); also elsewhere on the board
/D11: U1.24 (PB5); also elsewhere on the board
/D12: U1.25 (PB6); also elsewhere on the board
/D13: U1.26 (PB7); also elsewhere on the board
/D14: U1.64 (PJ1); also elsewhere on the board
/D15: U1.63 (PJ0); also elsewhere on the board
/D16: U1.12 (PH0); also elsewhere on the board
/D17: U1.13 (PH1); also elsewhere on the board
/D18: U1.46 (PD3); also elsewhere on the board
/D19: U1.45 (PD2); also elsewhere on the board
/D20: R90.1, U1.44 (PD1); also elsewhere on the board
/D21: R91.1, U1.43 (PD0); also elsewhere on the board
/D22: U1.78 (PA0); also elsewhere on the board
/D23: U1.77 (PA1); also elsewhere on the board
/D24: U1.76 (PA2); also elsewhere on the board
/D25: U1.75 (PA3); also elsewhere on the board
/D26: U1.74 (PA4); also elsewhere on the board
/D27: U1.73 (PA5); also elsewhere on the board
/D28: U1.72 (PA6); also elsewhere on the board
/D29: U1.71 (PA7); also elsewhere on the board
/D30: U1.60 (PC7); also elsewhere on the board
/D31: U1.59 (PC6); also elsewhere on the board
/D32: U1.58 (PC5); also elsewhere on the board
/D33: U1.57 (PC4); also elsewhere on the board
/D34: U1.56 (PC3); also elsewhere on the board
/D35: U1.55 (PC2); also elsewhere on the board
/D36: U1.54 (PC1); also elsewhere on the board
/D37: U1.53 (PC0); also elsewhere on the board
/D38: U1.50 (PD7); also elsewhere on the board
/D39: U1.70 (PG2); also elsewhere on the board
/D40: U1.52 (PG1); also elsewhere on the board
/D41: U1.51 (PG0); also elsewhere on the board
/D42: U1.42 (PL7); also elsewhere on the board
/D43: U1.41 (PL6); also elsewhere on the board
/D44: U1.40 (PL5); also elsewhere on the board
/D45: U1.39 (PL4); also elsewhere on the board
/D46: U1.38 (PL3); also elsewhere on the board
/D47: U1.37 (PL2); also elsewhere on the board
/D48: U1.36 (PL1); also elsewhere on the board
/D49: U1.35 (PL0); also elsewhere on the board
/D50: J16.1, U1.22 (PB3); also elsewhere on the board
/D51: J16.4, U1.21 (PB2); also elsewhere on the board
/D52: J16.3, U1.20 (PB1); also elsewhere on the board
/D53: U1.19 (PB0); also elsewhere on the board
/~mega2560_reset: C92.2, D3.2 (A), J16.5, R10.1, SW1.2, U1.30 (~RESET); also elsewhere on the board
GND: C1.1, C2.1, C3.2, C4.2, C5.2, C6.2, C7.2, C8.2, C92.1, J16.6, SW1.1, U1.11 (GND), U1.32 (GND), U1.62 (GND), U1.81 (GND), U1.99 (GND), Y1.2; also elsewhere on the board
unnamed: C8.1, L1.2, U1.100 (AVCC)
unnamed: C1.2, R9.2, U1.34 (XTAL1), Y1.1
unnamed: C2.2, R9.1, U1.33 (XTAL2), Y1.3

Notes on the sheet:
ICSP header

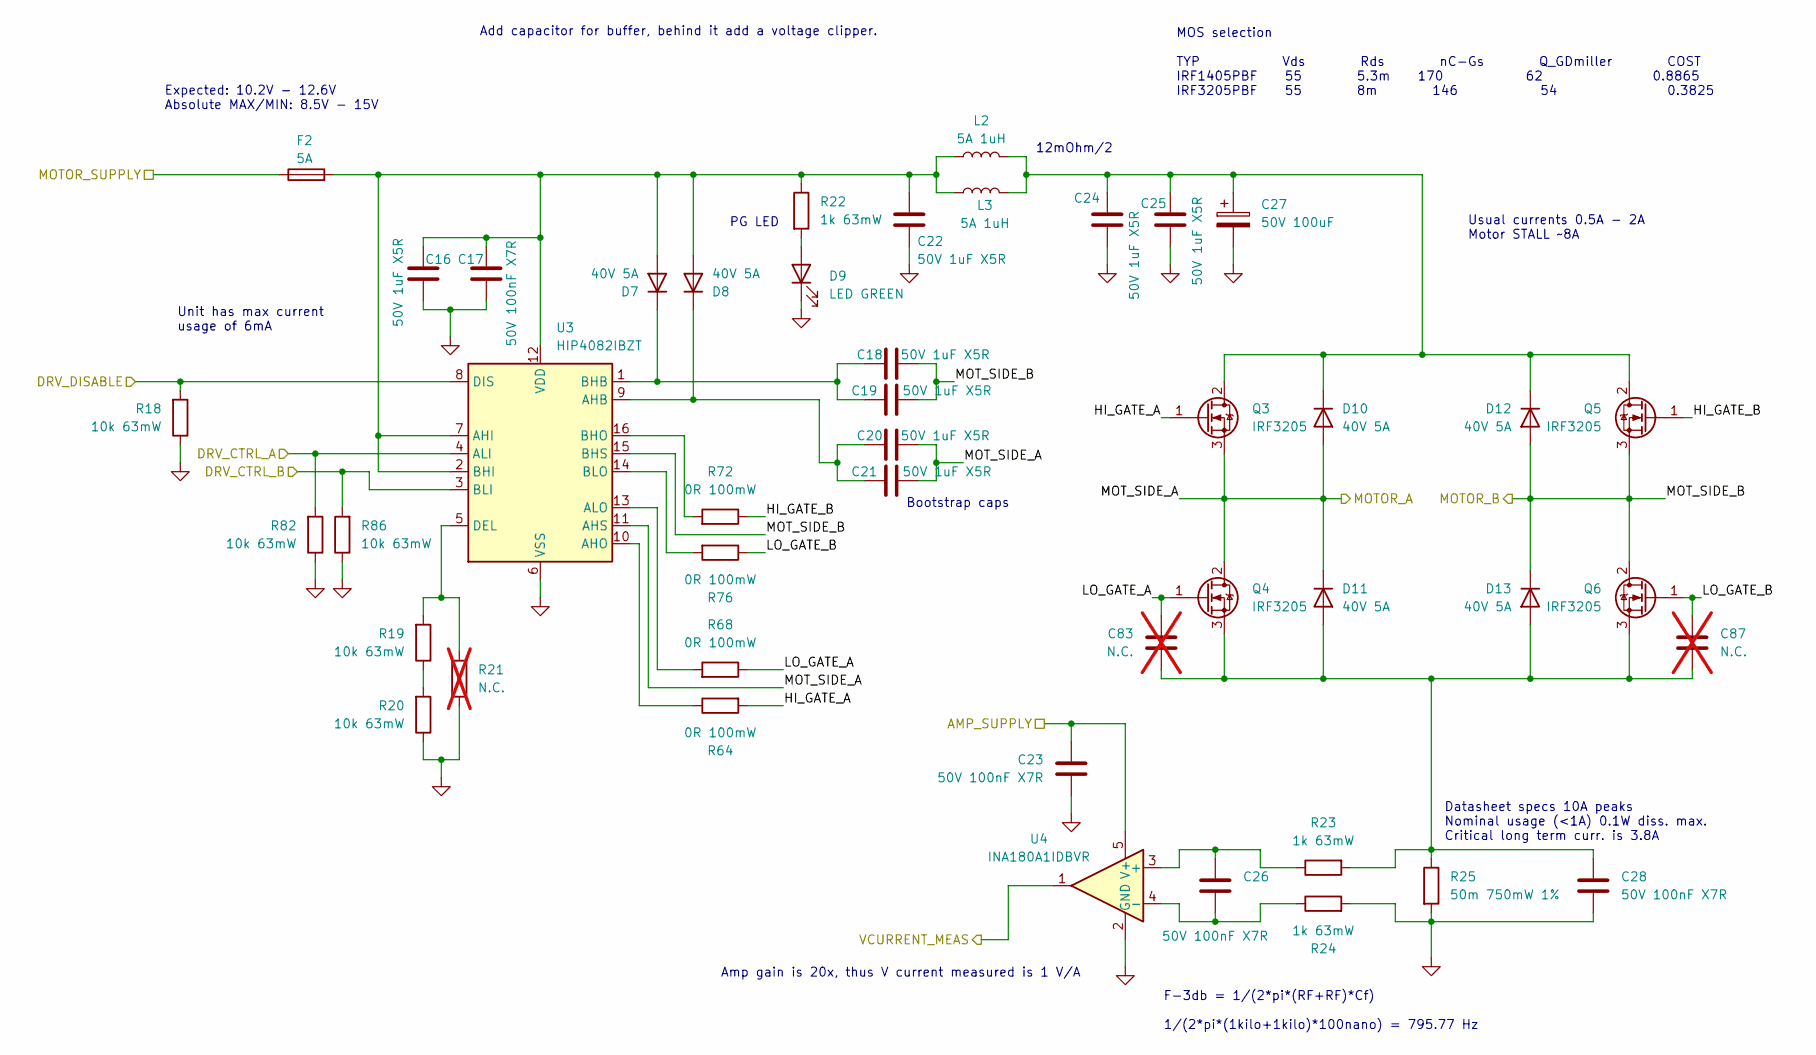
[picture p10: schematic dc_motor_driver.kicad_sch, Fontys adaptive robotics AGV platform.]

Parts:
C16, C18, C19, C20, C21, C22, C24, C25: 50V 1uF X5R; C_0603_1608Metric; LCSC C15849
C17, C23, C26, C28: 50V 100nF X7R; C_0603_1608Metric; LCSC C14663
C27: 50V 100uF; CP_Elec_8x10.5; LCSC C5246561
C83, C87: N.C.; C_0603_1608Metric; not fitted
D7, D8, D10, D11, D12, D13: 40V 5A; D_SMA; LCSC C22452
D9: LED GREEN; LED_0805_2012Metric; LCSC C2297
F2: 5A; BLX-A fuse holder
L2, L3: 5A 1uH; L_APV_ANR5040; LCSC C167953
Q3, Q4, Q5, Q6: IRF3205; TO-220-3_Horizontal_TabDown; LCSC C2561
R18, R19, R20, R82, R86: 10k 63mW; R_0402_1005Metric; LCSC C25744
R21: N.C.; R_0402_1005Metric; LCSC C25744; not fitted
R22, R23, R24: 1k 63mW; R_0402_1005Metric; LCSC C11702
R25: 50m 750mW 1%; R_2512_6332Metric; LCSC C127698
R64, R68, R72, R76: 0R 100mW; R_0603_1608Metric; LCSC C21189
U3: HIP4082IBZT; SOIC-16_3.9x9.9mm_P1.27mm; LCSC C50123
U4: INA180A1IDBVR; SOT-23-5; LCSC C122228

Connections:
+5V: C23.2, U4.5 (V+); also elsewhere on the board
+BATT: F2.1; also elsewhere on the board
/MOT_CURR_V_1: U4.1
/MOT_DRV_DISABLE: R18.2, U3.8 (DIS); also elsewhere on the board
/MOT_DRV_PWM_A1: R82.2, U3.4 (ALI)
/MOT_DRV_PWM_B1: R86.2, U3.3 (BLI)
/Motor driver 1/HI_GATE_A: Q3.1 (G), R64.2
/Motor driver 1/HI_GATE_B: Q5.1 (G), R72.1
/Motor driver 1/LO_GATE_A: C83.2, Q4.1 (G), R68.1
/Motor driver 1/LO_GATE_B: C87.2, Q6.1 (G), R76.1
/Motor driver 1/MOT_SIDE_A: C20.2, C21.2, D10.2 (A), D11.1 (K), Q3.3 (S), Q4.2 (D), U3.11 (AHS); also elsewhere on the board
/Motor driver 1/MOT_SIDE_B: C18.2, C19.2, D12.2 (A), D13.1 (K), Q5.3 (S), Q6.2 (D), U3.15 (BHS); also elsewhere on the board
GND: C16.2, C17.1, C22.2, C23.1, C24.2, C25.2, C27.2, C28.1, D9.1 (K), R18.1, R20.1, R21.1, R24.2, R25.2, R82.1, R86.1, U3.6 (VSS), U4.2 (GND); also elsewhere on the board
unnamed: C16.1, C17.2, C22.1, D7.2 (A), D8.2 (A), F2.2, L2.1, L3.2, R22.1, U3.2 (BHI), U3.7 (AHI), U3.12 (VDD)
unnamed: C18.1, C19.1, D7.1 (K), U3.1 (BHB)
unnamed: C20.1, C21.1, D8.1 (K), U3.9 (AHB)
unnamed: D9.2 (A), R22.2
unnamed: C24.1, C25.1, C27.1, D10.1 (K), D12.1 (K), L2.2, L3.1, Q3.2 (D), Q5.2 (D)
unnamed: C28.2, C83.1, C87.1, D11.2 (A), D13.2 (A), Q4.3 (S), Q6.3 (S), R23.2, R25.1
unnamed: R19.1, R20.2
unnamed: R64.1, U3.10 (AHO)
unnamed: R68.2, U3.13 (ALO)
unnamed: R72.2, U3.16 (BHO)
unnamed: R76.2, U3.14 (BLO)
unnamed: R19.2, R21.2, U3.5 (DEL)
unnamed: C26.2, R23.1, U4.3 (+)
unnamed: C26.1, R24.1, U4.4 (-)

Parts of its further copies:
C35, C37, C38, C39, C40, C41, C43, C44, C48, C50, C51, C52, C53, C54, C56, C57, C61, C63, C64, C65, C66, C67, C69, C70: 50V 1uF X5R; C_0603_1608Metric; LCSC C15849
C36, C42, C45, C47, C49, C55, C58, C60, C62, C68, C71, C73: 50V 100nF X7R; C_0603_1608Metric; LCSC C14663
C46, C59, C72: 50V 100uF; CP_Elec_8x10.5; LCSC C5246561
C84, C85, C86, C88, C89, C90: N.C.; C_0603_1608Metric; not fitted
D15, D16, D18, D19, D20, D21, D22, D23, D25, D26, D27, D28, D29, D30, D32, D33, D34, D35: 40V 5A; D_SMA; LCSC C22452
D17, D24, D31: LED GREEN; LED_0805_2012Metric; LCSC C2297
F3, F4, F5: 5A; BLX-A fuse holder
L5, L6, L7, L8, L9, L10: 5A 1uH; L_APV_ANR5040; LCSC C167953
Q7, Q8, Q9, Q10, Q11, Q12, Q13, Q14, Q15, Q16, Q17, Q18: IRF3205; TO-220-3_Horizontal_TabDown; LCSC C2561
R30, R31, R32, R38, R39, R40, R46, R47, R48, R83, R84, R85, R87, R88, R89: 10k 63mW; R_0402_1005Metric; LCSC C25744
R33, R41, R49: N.C.; R_0402_1005Metric; LCSC C25744; not fitted
R34, R35, R36, R42, R43, R44, R50, R51, R52: 1k 63mW; R_0402_1005Metric; LCSC C11702
R37, R45, R53: 50m 750mW 1%; R_2512_6332Metric; LCSC C127698
R65, R66, R67, R69, R70, R71, R73, R74, R75, R77, R78, R79: 0R 100mW; R_0603_1608Metric; LCSC C21189
U6, U8, U10: HIP4082IBZT; SOIC-16_3.9x9.9mm_P1.27mm; LCSC C50123
U7, U9, U11: INA180A1IDBVR; SOT-23-5; LCSC C122228

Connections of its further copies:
+5V: C42.2, C55.2, C68.2, U7.5 (V+), U9.5 (V+), U11.5 (V+); also elsewhere on the board
+BATT: F3.1, F4.1, F5.1; also elsewhere on the board
/MOT_CURR_V_2: U7.1
/MOT_CURR_V_3: U9.1
/MOT_CURR_V_4: U11.1
/MOT_DRV_DISABLE: R30.2, R38.2, R46.2, U6.8 (DIS), U8.8 (DIS), U10.8 (DIS); also elsewhere on the board
/MOT_DRV_PWM_A2: R83.2, U6.4 (ALI)
/MOT_DRV_PWM_A3: R84.2, U8.4 (ALI)
/MOT_DRV_PWM_A4: R85.2, U10.4 (ALI)
/MOT_DRV_PWM_B2: R87.2, U6.3 (BLI)
/MOT_DRV_PWM_B3: R88.2, U8.3 (BLI)
/MOT_DRV_PWM_B4: R89.2, U10.3 (BLI)
/Motor driver 2/HI_GATE_A: Q7.1 (G), R65.2
/Motor driver 2/HI_GATE_B: Q9.1 (G), R73.1
/Motor driver 2/LO_GATE_A: C84.2, Q8.1 (G), R69.1
/Motor driver 2/LO_GATE_B: C88.2, Q10.1 (G), R77.1
/Motor driver 2/MOT_SIDE_A: C39.2, C40.2, D18.2 (A), D19.1 (K), Q7.3 (S), Q8.2 (D), U6.11 (AHS); also elsewhere on the board
/Motor driver 2/MOT_SIDE_B: C37.2, C38.2, D20.2 (A), D21.1 (K), Q9.3 (S), Q10.2 (D), U6.15 (BHS); also elsewhere on the board
/Motor driver 3/HI_GATE_A: Q11.1 (G), R66.2
/Motor driver 3/HI_GATE_B: Q13.1 (G), R74.1
/Motor driver 3/LO_GATE_A: C85.2, Q12.1 (G), R70.1
/Motor driver 3/LO_GATE_B: C89.2, Q14.1 (G), R78.1
/Motor driver 3/MOT_SIDE_A: C52.2, C53.2, D25.2 (A), D26.1 (K), Q11.3 (S), Q12.2 (D), U8.11 (AHS); also elsewhere on the board
/Motor driver 3/MOT_SIDE_B: C50.2, C51.2, D27.2 (A), D28.1 (K), Q13.3 (S), Q14.2 (D), U8.15 (BHS); also elsewhere on the board
/Motor driver 4/HI_GATE_A: Q15.1 (G), R67.2
/Motor driver 4/HI_GATE_B: Q17.1 (G), R75.1
/Motor driver 4/LO_GATE_A: C86.2, Q16.1 (G), R71.1
/Motor driver 4/LO_GATE_B: C90.2, Q18.1 (G), R79.1
/Motor driver 4/MOT_SIDE_A: C65.2, C66.2, D32.2 (A), D33.1 (K), Q15.3 (S), Q16.2 (D), U10.11 (AHS); also elsewhere on the board
/Motor driver 4/MOT_SIDE_B: C63.2, C64.2, D34.2 (A), D35.1 (K), Q17.3 (S), Q18.2 (D), U10.15 (BHS); also elsewhere on the board
GND: C35.2, C36.1, C41.2, C42.1, C43.2, C44.2, C46.2, C47.1, C48.2, C49.1, C54.2, C55.1, C56.2, C57.2, C59.2, C60.1, C61.2, C62.1, C67.2, C68.1, C69.2, C70.2, C72.2, C73.1, D17.1 (K), D24.1 (K), D31.1 (K), R30.1, R32.1, R33.1, R36.2, R37.2, R38.1, R40.1, R41.1, R44.2, R45.2, R46.1, R48.1, R49.1, R52.2, R53.2, R83.1, R84.1, R85.1, R87.1, R88.1, R89.1, U6.6 (VSS), U7.2 (GND), U8.6 (VSS), U9.2 (GND), U10.6 (VSS), U11.2 (GND); also elsewhere on the board
unnamed: C35.1, C36.2, C41.1, D15.2 (A), D16.2 (A), F3.2, L5.1, L6.2, R34.1, U6.2 (BHI), U6.7 (AHI), U6.12 (VDD)
unnamed: C37.1, C38.1, D15.1 (K), U6.1 (BHB)
unnamed: C39.1, C40.1, D16.1 (K), U6.9 (AHB)
unnamed: D17.2 (A), R34.2
unnamed: C43.1, C44.1, C46.1, D18.1 (K), D20.1 (K), L5.2, L6.1, Q7.2 (D), Q9.2 (D)
unnamed: C47.2, C84.1, C88.1, D19.2 (A), D21.2 (A), Q8.3 (S), Q10.3 (S), R35.2, R37.1
unnamed: C48.1, C49.2, C54.1, D22.2 (A), D23.2 (A), F4.2, L7.1, L8.2, R42.1, U8.2 (BHI), U8.7 (AHI), U8.12 (VDD)
unnamed: C50.1, C51.1, D22.1 (K), U8.1 (BHB)
unnamed: C52.1, C53.1, D23.1 (K), U8.9 (AHB)
unnamed: D24.2 (A), R42.2
unnamed: C56.1, C57.1, C59.1, D25.1 (K), D27.1 (K), L7.2, L8.1, Q11.2 (D), Q13.2 (D)
unnamed: C60.2, C85.1, C89.1, D26.2 (A), D28.2 (A), Q12.3 (S), Q14.3 (S), R43.2, R45.1
unnamed: C61.1, C62.2, C67.1, D29.2 (A), D30.2 (A), F5.2, L9.1, L10.2, R50.1, U10.2 (BHI), U10.7 (AHI), U10.12 (VDD)
unnamed: C63.1, C64.1, D29.1 (K), U10.1 (BHB)
unnamed: C65.1, C66.1, D30.1 (K), U10.9 (AHB)
unnamed: D31.2 (A), R50.2
unnamed: C69.1, C70.1, C72.1, D32.1 (K), D34.1 (K), L9.2, L10.1, Q15.2 (D), Q17.2 (D)
unnamed: C73.2, C86.1, C90.1, D33.2 (A), D35.2 (A), Q16.3 (S), Q18.3 (S), R51.2, R53.1
unnamed: R31.1, R32.2
unnamed: R39.1, R40.2
unnamed: R47.1, R48.2
unnamed: R65.1, U6.10 (AHO)
unnamed: R69.2, U6.13 (ALO)
unnamed: R73.2, U6.16 (BHO)
unnamed: R77.2, U6.14 (BLO)
unnamed: R31.2, R33.2, U6.5 (DEL)
unnamed: C45.2, R35.1, U7.3 (+)
unnamed: C45.1, R36.1, U7.4 (-)
unnamed: R66.1, U8.10 (AHO)
unnamed: R70.2, U8.13 (ALO)
unnamed: R74.2, U8.16 (BHO)
unnamed: R78.2, U8.14 (BLO)
unnamed: R39.2, R41.2, U8.5 (DEL)
unnamed: C58.2, R43.1, U9.3 (+)
unnamed: C58.1, R44.1, U9.4 (-)
unnamed: R67.1, U10.10 (AHO)
unnamed: R71.2, U10.13 (ALO)
unnamed: R75.2, U10.16 (BHO)
unnamed: R79.2, U10.14 (BLO)
unnamed: R47.2, R49.2, U10.5 (DEL)
unnamed: C71.2, R51.1, U11.3 (+)
unnamed: C71.1, R52.1, U11.4 (-)

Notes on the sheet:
Usual currents 0.5A - 2A Motor STALL ~8A
PG LED
Expected: 10.2V - 12.6V Absolute MAX/MIN: 8.5V - 15V
F-3db = 1/(2*pi*(RF+RF)*Cf) 1/(2*pi*(1kilo+1kilo)*100nano) = 795.77 Hz
Bootstrap caps
Amp gain is 20x, thus V current measured is 1 V/A
Add capacitor for buffer, behind it add a voltage clipper.
12mOhm/2
Datasheet specs 10A peaks Nominal usage (<1A) 0.1W diss. max. Critical long term curr. is 3.8A
MOS selection TYP Vds Rds nC-Gs Q_GDmiller COST IRF1405PBF 55 5.3m 170 62 0.8865 IRF3205PBF 55 8m 146 54 0.3825
Unit has max current usage of 6mA

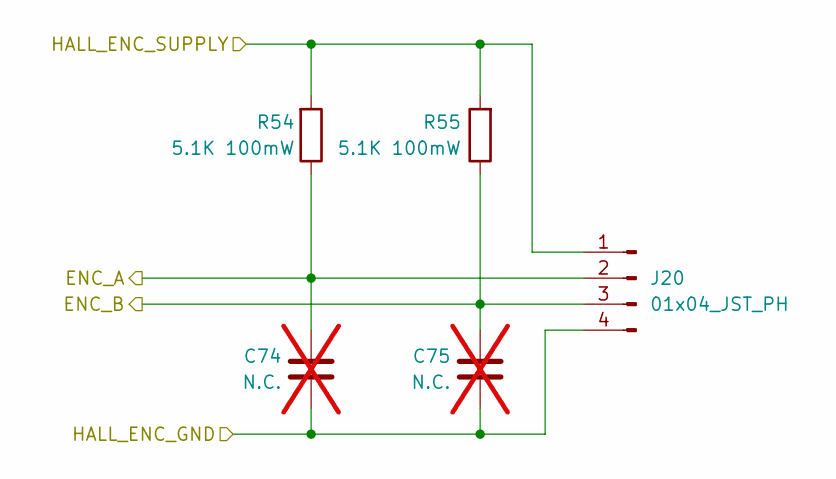
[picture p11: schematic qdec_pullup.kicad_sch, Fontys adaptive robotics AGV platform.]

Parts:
C74, C75: N.C.; C_0603_1608Metric; not fitted
J20: 01x04_JST_PH; JST_PH_B4B-PH-K_1x04_P2.00mm_Vertical
R54, R55: 5.1K 100mW; C_0603_1608Metric; LCSC C23186

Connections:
+5V: J20.1, R54.2, R55.2; also elsewhere on the board
/ENC_A1: C74.2, J20.2, R54.1
/ENC_B1: C75.2, J20.3, R55.1
GND: C74.1, C75.1, J20.4; also elsewhere on the board

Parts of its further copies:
C76, C77, C78, C79, C80, C81: N.C.; C_0603_1608Metric; not fitted
J21, J22, J23: 01x04_JST_PH; JST_PH_B4B-PH-K_1x04_P2.00mm_Vertical
R56, R57, R58, R59, R60, R61: 5.1K 100mW; C_0603_1608Metric; LCSC C23186

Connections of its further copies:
+5V: J21.1, J22.1, J23.1, R56.2, R57.2, R58.2, R59.2, R60.2, R61.2; also elsewhere on the board
/ENC_A2: C76.2, J21.2, R56.1
/ENC_A3: C78.2, J22.2, R58.1
/ENC_A4: C80.2, J23.2, R60.1
/ENC_B2: C77.2, J21.3, R57.1
/ENC_B3: C79.2, J22.3, R59.1
/ENC_B4: C81.2, J23.3, R61.1
GND: C76.1, C77.1, C78.1, C79.1, C80.1, C81.1, J21.4, J22.4, J23.4; also elsewhere on the board

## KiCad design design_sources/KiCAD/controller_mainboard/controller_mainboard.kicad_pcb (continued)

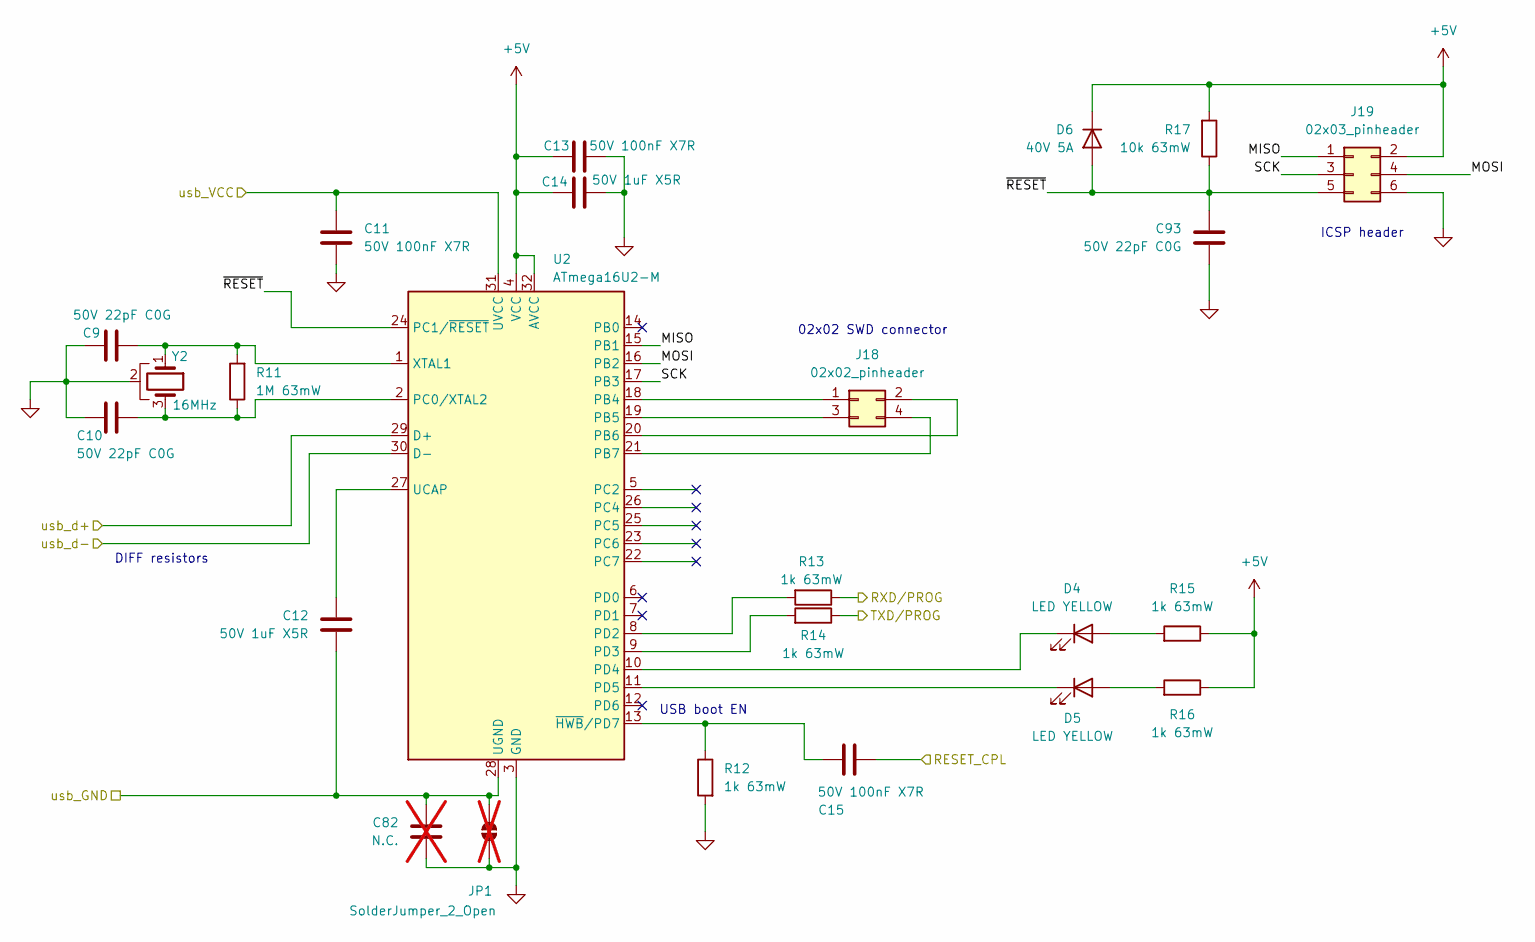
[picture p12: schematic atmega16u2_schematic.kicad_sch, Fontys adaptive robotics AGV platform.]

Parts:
C9, C10, C93: 50V 22pF C0G; C_0402_1005Metric; LCSC C1555
C11, C13, C15: 50V 100nF X7R; C_0603_1608Metric; LCSC C14663
C12, C14: 50V 1uF X5R; C_0603_1608Metric; LCSC C15849
C82: N.C.; C_0603_1608Metric; not fitted
D4, D5: LED YELLOW; LED_0603_1608Metric; LCSC C72038
D6: 40V 5A; D_SMA; LCSC C22452
J18: 02x02_pinheader; PinHeader_2x02_P2.54mm_Vertical
J19: 02x03_pinheader; PinHeader_2x03_P2.54mm_Vertical
JP1: SolderJumper_2_Open; SolderJumper-2_P1.3mm_Open_RoundedPad1.0x1.5mm; not fitted
R11: 1M 63mW; R_0603_1608Metric; LCSC C22935
R12, R13, R14, R15, R16: 1k 63mW; R_0402_1005Metric; LCSC C11702
R17: 10k 63mW; R_0402_1005Metric; LCSC C25744
U2: ATmega16U2-M; QFN-32-1EP_5x5mm_P0.5mm_EP3.1x3.1mm; LCSC C17317
Y2: 16MHz; Resonator_SMD_Murata_CSTxExxV-3Pin_3.0x1.1mm; LCSC C783275

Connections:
+5V: C13.1, C14.1, D6.1 (K), J19.2, R15.1, R16.1, R17.2, U2.4 (VCC), U2.32 (AVCC); also elsewhere on the board
/ATmega16u2/MISO: J19.1, U2.15 (PB1)
/ATmega16u2/MOSI: J19.4, U2.16 (PB2)
/ATmega16u2/SCK: J19.3, U2.17 (PB3)
/ATmega16u2/~RESET: C93.2, D6.2 (A), J19.5, R17.1, U2.24 (PC1/~RESET)
/D0: R14.1; also elsewhere on the board
/D1: R13.1; also elsewhere on the board
/USB_D_N: U2.30 (D-); also elsewhere on the board
/USB_D_P: U2.29 (D+); also elsewhere on the board
/USB_GND: C12.2, C82.2, JP1.2 (B), U2.28 (UGND); also elsewhere on the board
/USB_VBUS: C11.1, U2.31 (UVCC); also elsewhere on the board
/~mega2560_reset: C15.2; also elsewhere on the board
GND: C9.1, C10.1, C11.2, C13.2, C14.2, C82.1, C93.1, J19.6, JP1.1 (A), R12.2, U2.3 (GND), U2.33 (GND), Y2.2; also elsewhere on the board
unnamed: D4.2 (A), R15.2
unnamed: D4.1 (K), U2.10 (PD4)
unnamed: D5.2 (A), R16.2
unnamed: D5.1 (K), U2.11 (PD5)
unnamed: J18.1, U2.18 (PB4)
unnamed: J18.2, U2.20 (PB6)
unnamed: J18.3, U2.19 (PB5)
unnamed: J18.4, U2.21 (PB7)
unnamed: C10.2, R11.1, U2.2 (PC0/XTAL2), Y2.3
unnamed: R13.2, U2.8 (PD2)
unnamed: R14.2, U2.9 (PD3)
unnamed: C12.1, U2.27 (UCAP)
unnamed: C9.2, R11.2, U2.1 (XTAL1), Y2.1
unnamed: C15.1, R12.1, U2.13 (~HWB/PD7)

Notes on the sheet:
02x02 SWD connector
USB boot EN
DIFF resistors
ICSP header

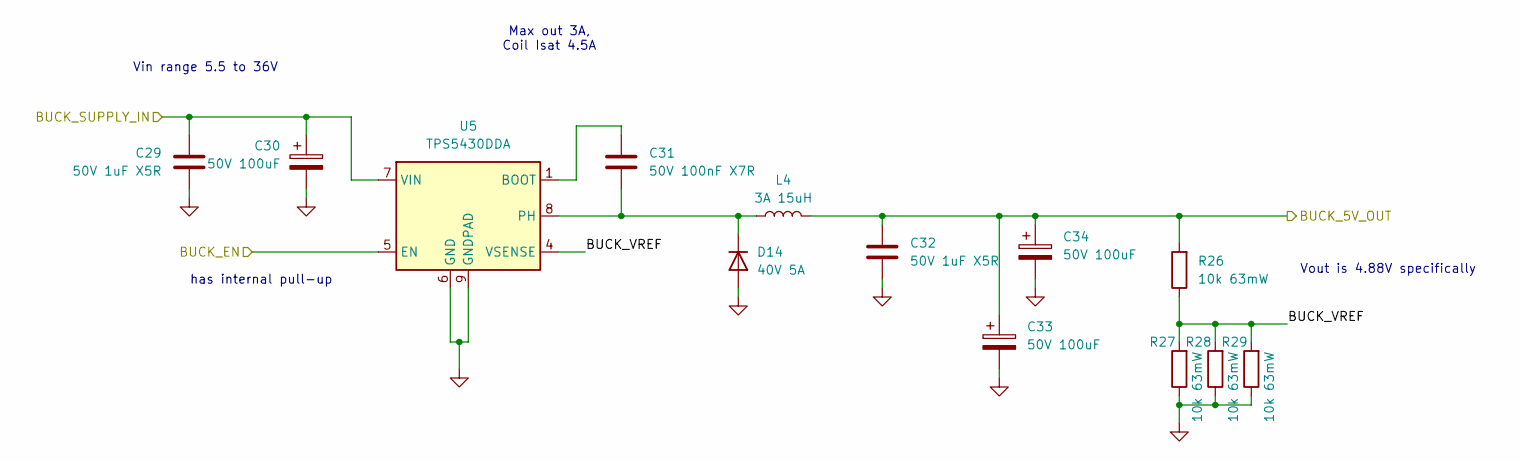
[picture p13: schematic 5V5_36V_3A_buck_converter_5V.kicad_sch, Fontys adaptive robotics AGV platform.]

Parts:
C29, C32: 50V 1uF X5R; C_0603_1608Metric; LCSC C15849
C30, C33, C34: 50V 100uF; CP_Elec_8x10.5; LCSC C5246561
C31: 50V 100nF X7R; C_0603_1608Metric; LCSC C14663
D14: 40V 5A; D_SMA; LCSC C22452
L4: 3A 15uH; L_APV_APH0630; LCSC C177243
R26, R27, R28, R29: 10k 63mW; R_0402_1005Metric; LCSC C25744
U5: TPS5430DDA; TI_SO-PowerPAD-8_ThermalVias; LCSC C9864

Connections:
+5V: C32.1, C33.1, C34.1, L4.2, R26.2; also elsewhere on the board
+BATT: C29.1, C30.1, U5.7 (VIN); also elsewhere on the board
/5V_3A_buck_converter/BUCK_EN: U5.5 (EN); also elsewhere on the board
/5V_3A_buck_converter/BUCK_VREF: R26.1, R27.2, R28.2, R29.2, U5.4 (VSENSE)
GND: C29.2, C30.2, C32.2, C33.2, C34.2, D14.2 (A), R27.1, R28.1, R29.1, U5.6 (GND), U5.9 (GNDPAD); also elsewhere on the board
unnamed: C31.2, D14.1 (K), L4.1, U5.8 (PH)
unnamed: C31.1, U5.1 (BOOT)

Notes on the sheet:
Vout is 4.88V specifically
has internal pull-up
Max out 3A, Coil Isat 4.5A
Vin range 5.5 to 36V

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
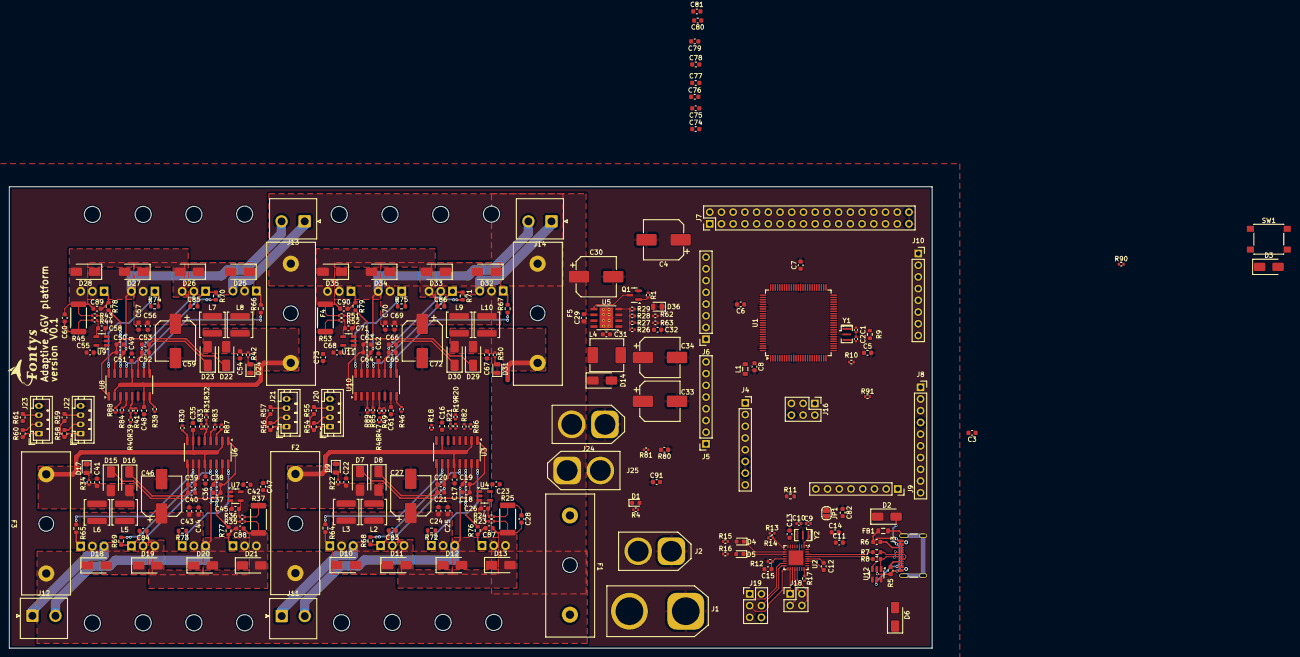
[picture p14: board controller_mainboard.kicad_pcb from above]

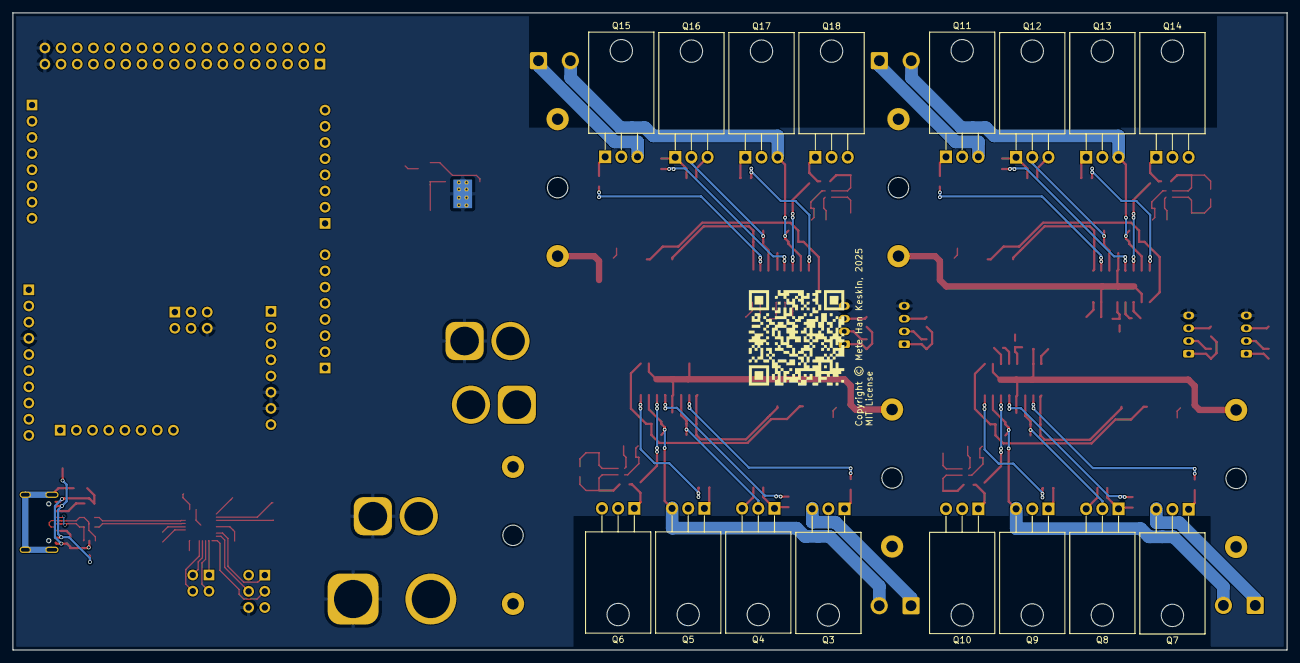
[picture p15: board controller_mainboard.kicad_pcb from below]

Board: 4 copper layers, 200.0 x 100.0 mm, 288 parts (16 on the bottom side), 211 nets.

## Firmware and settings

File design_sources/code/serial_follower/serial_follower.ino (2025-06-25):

/* WARNING, CODE IS INCOMPLETE, IT IS UP TO YOU TO COMPLETE IT */

/* ========================
      Pin Definitions 
 ======================== */

/* --- Encoder Inputs --- */
#define ENC_B4 22
#define ENC_A4 23
#define ENC_B3 24
#define ENC_A3 25
#define ENC_B2 26
#define ENC_A2 27
#define ENC_B1 28
#define ENC_A1 29

/* --- Motor Driver PWM Outputs --- */
#define MOT_DRV_PWM_B4 2
#define MOT_DRV_PWM_A4 3
#define MOT_DRV_PWM_B2 4
#define MOT_DRV_PWM_A2 5
#define MOT_DRV_PWM_A3 6
#define MOT_DRV_PWM_B3 7
#define MOT_DRV_PWM_A1 8
#define MOT_DRV_PWM_B1 9

/* --- Analog Inputs --- */
#define VBAT_ADC A3
#define MOT_CURR_V_1 A4
#define MOT_CURR_V_2 A5
#define MOT_CURR_V_3 A6
#define MOT_CURR_V_4 A7

/*
  === STUDENT TEMPLATE START ===

  This Arduino code handles serial communication with a master device.

  Serial Command Structure:
    [CMD][ARG1][ARG2]...

  Implemented Commands:
    0x01: Echo back 1 byte
    0x02: Set a GPIO pin HIGH/LOW
    0x03: Read a GPIO pin's state
    0x04: Read ADC value from analog pin
    0x05: Set PWM output on any PWM-capable pin

  Extend this sketch to:
    - Add encoder reading support
    - Add additional motor control logic
    - Implement safety or timing mechanisms

  NOTE: Ensure pin numbers are valid on your board. Use digital pins 0-53 and analog pins A0-A15.
        Use the PCBA schematic as reference. 

  === STUDENT TEMPLATE END ===
*/

void setup() {
  Serial.begin(115200);
}

/*  =====================================
                  Main Loop
    ===================================== */

void loop() {
  if (Serial.available()) {
    uint8_t command = Serial.read();

    /* */
    switch (command) {
      case 0x01: handleEcho(); break;
      case 0x02: handleSetGPIO(); break;
      case 0x03: handleReadGPIO(); break;
      case 0x04: handleReadADC(); break;
      case 0x05: handleSetPWM(); break;
      default: handleUnknownCommand(); break;
    }
  }
}



// =====================================
// Command Handlers
// =====================================
void handleEcho() {
  waitForBytes(1);
  uint8_t value = Serial.read();
  Serial.write(0x81);
  Serial.write(value);
}

void handleSetGPIO() {
  waitForBytes(2);
  uint8_t pin = Serial.read();
  uint8_t val = Serial.read();
  pinMode(pin, OUTPUT);
  digitalWrite(pin, val ? HIGH : LOW);
  Serial.write(0x82);
  Serial.write(pin);
  Serial.write(val);
}

void handleReadGPIO() {
  waitForBytes(1);
  uint8_t pin = Serial.read();
  pinMode(pin, INPUT);
  uint8_t val = digitalRead(pin);
  Serial.write(0x83);
  Serial.write(pin);
  Serial.write(val);
}

void handleReadADC() {
  waitForBytes(1);
  uint8_t analogPin = Serial.read();
  int adcVal = analogRead(analogPin);
  Serial.write(0x84);
  Serial.write(analogPin);
  Serial.write(highByte(adcVal));
  Serial.write(lowByte(adcVal));
}

void handleSetPWM() {
  waitForBytes(2);
  uint8_t pin = Serial.read();
  uint8_t pwmVal = Serial.read();
  pinMode(pin, OUTPUT);
  analogWrite(pin, pwmVal);
  Serial.write(0x85);
  Serial.write(pin);
  Serial.write(pwmVal);
}

void handleUnknownCommand() {
  Serial.write(0xFF);  // Error or unsupported command
}

// =====================================
// Utility
// =====================================
void waitForBytes(uint8_t n) {
  while (Serial.available() < n) {
    // Busy-wait (could be replaced with timeout for robustness)
  }
}

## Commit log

2025-03-01 WIP First commit, added atmega2560,atmega16u2, motor driver and root schematic sheet
    [atmega16u2_schematic.kicad_sch, atmega2560_schematic.kicad_sch, controller_mainboard.kicad_pcb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]
2025-03-01 Commit after closing kicad
    [controller_mainboard.kicad_sch]
2025-03-02 Populated the schematic more, added buck.
    [5V5_36V_3A_buck_converter_5V.kicad_sch, controller_mainboard.csv, controller_mainboard.kicad_sch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]
2025-03-02 Continued development on the schematic. Pins wired. TODO validate.
    [5V5_36V_3A_buck_converter_5V.kicad_sch, atmega16u2_schematic.kicad_sch, atmega2560_schematic.kicad_sch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]
2025-03-03 Added ESD protection ic, added footprints to all IC and loaded into pcbnew to size up the pcb size.
    [5V5_36V_3A_buck_converter_5V.kicad_sch, atmega16u2_schematic.kicad_sch, atmega2560_schematic.kicad_sch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]
2025-03-03 Read through schematic to bugfix.
    [atmega16u2_schematic.kicad_sch, atmega2560_schematic.kicad_sch, controller_mainboard.kicad_sch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]
2025-03-03 Adjusted gitignore to ignore backups, removed backup files
    [atmega16u2_schematic.kicad_sch, atmega2560_schematic.kicad_sch, controller_mainboard.kicad_pcb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]
2025-03-03 started initial pcb layout
    [controller_mainboard.kicad_pcb, dc_motor_driver.kicad_sch]
2025-03-03 Slight schematic adjustments and continue on draft pcb layout
    [atmega16u2_schematic.kicad_sch, controller_mainboard.kicad_pcb]
2025-03-04 Removed backups again, improved the PCB layout
    [controller_mainboard.kicad_pcb, controller_mainboard.kicad_sch]
2025-03-09 Made layout of motor driver ch1, will replicate layout on other channels next.
    [controller_mainboard.kicad_pcb]
2025-03-09 Major PCB layout progress, motor drivers are routed and placed. PCB dimensions set, started ATMEGA2560 layout. Slight schematic fixes.
    [controller_mainboard.kicad_pcb, controller_mainboard.kicad_sch]
2025-03-09 Advanced the hardware layout further.
    [atmega16u2_schematic.kicad_sch, atmega2560_schematic.kicad_sch, controller_mainboard.kicad_sch]
2025-04-03 Nearly finalized hardware layout. TODO add extra GND stitching vias, label IO numbers on silk, add cool silk drawings
    [controller_mainboard.kicad_sch]
2025-04-05 Added via&silk naming job done, added PCBA renders
    [controller_mainboard.kicad_sch]
2025-04-06 Generated inital production files for quotation.
    [bom.csv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]
2025-05-07 Added a spreadsheet of parts to source outside of LCSC
    [controller_board_v1.ods]
2025-06-15 Re-checked DRC, differing footprint warnings are fine, added production files for JLC placement and prod. TODO, maybe cool silk art at the bottom and definitive order list.
    [atmega16u2_schematic.kicad_sch, atmega2560_schematic.kicad_sch, bom.csv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]
2025-06-17 writing a readme file with instructions on ordering, also wrote down discrepancies on bom vs part etc.
2025-06-17 Backup commit, will change the bom and pos file errors
2025-06-17 Changed JLCPCB field to LCSC
    [5V5_36V_3A_buck_converter_5V.kicad_sch, atmega16u2_schematic.kicad_sch, atmega2560_schematic.kicad_sch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]
2025-06-17 re-generated production files after fixing lcsc field on PCB design
    [bom.csv]
2025-06-17 Updated 50m750mW resistor lcsc mpn number, re-generated production files
    [bom.csv, dc_motor_driver.kicad_sch]
2025-06-19 Changed kicad source folder name to contain board version number, also changed 3D model of the female XT-60's to match.
    [5V5_36V_3A_buck_converter_5V.kicad_sch, atmega16u2_schematic.kicad_sch, atmega2560_schematic.kicad_sch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]
2025-06-20 Added 11th step in producting ordering recipe for tinytronics assy
    [controller_board_v0_1.ods, controller_board_v1.ods]
2025-06-25 Expanded board spec file
2025-06-25 Renamed the spec file to the board design version

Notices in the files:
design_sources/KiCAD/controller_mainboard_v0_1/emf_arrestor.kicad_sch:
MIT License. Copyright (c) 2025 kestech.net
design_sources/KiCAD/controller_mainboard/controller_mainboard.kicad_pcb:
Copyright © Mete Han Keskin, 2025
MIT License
